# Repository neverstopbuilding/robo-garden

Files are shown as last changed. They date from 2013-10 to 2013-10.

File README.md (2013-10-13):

#RoboGarden

An open source garden hacking project. A robot that will take care of my plants, because I can't. 

Blog posts relating to the development of this project can be found at [http://neverstopbuilding.net/blog/categories/robo-garden](http://neverstopbuilding.net/blog/categories/robo-garden)

##License
<br /><span xmlns:dct="http://purl.org/dc/terms/" property="dct:title">RoboGarden</span> by <span xmlns:cc="http://creativecommons.org/ns#" property="cc:attributionName">Jason Fox</span> is licensed under a <a rel="license" href="http://creativecommons.org/licenses/by-nc-sa/3.0/deed.en_US">Creative Commons Attribution-NonCommercial-ShareAlike 3.0 Unported License</a>.

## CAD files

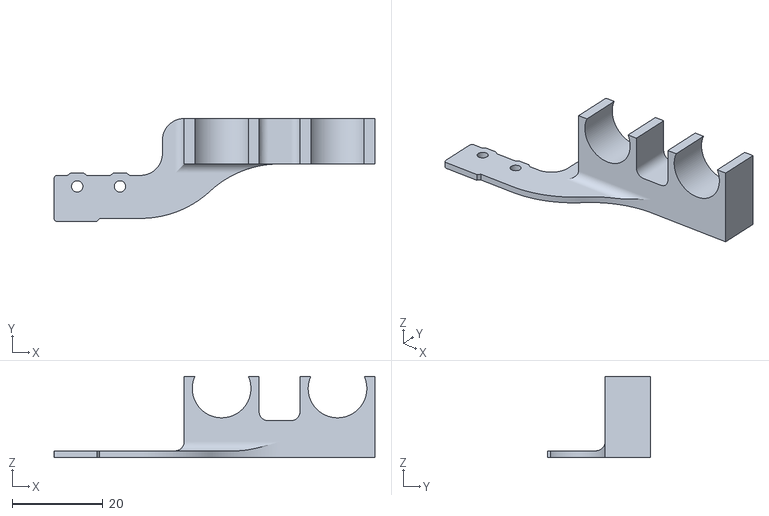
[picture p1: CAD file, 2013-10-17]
3d-parts/micro-clip.stl
70.6 x 22.6 x 17.9

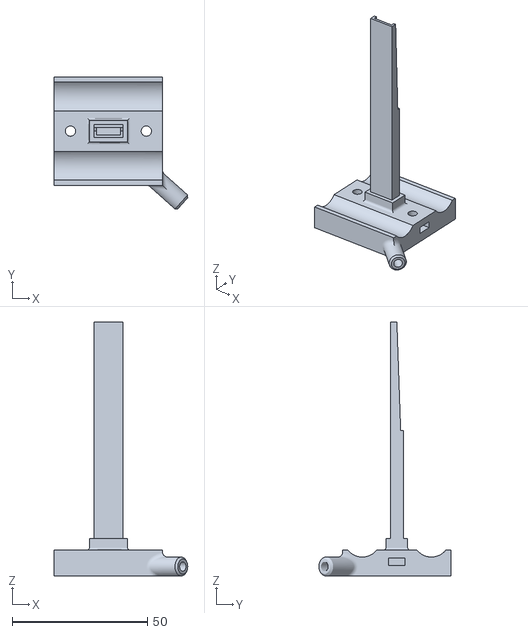
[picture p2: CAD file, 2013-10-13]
3d-parts/carriage-back.stl
49.3 x 48.8 x 93.8

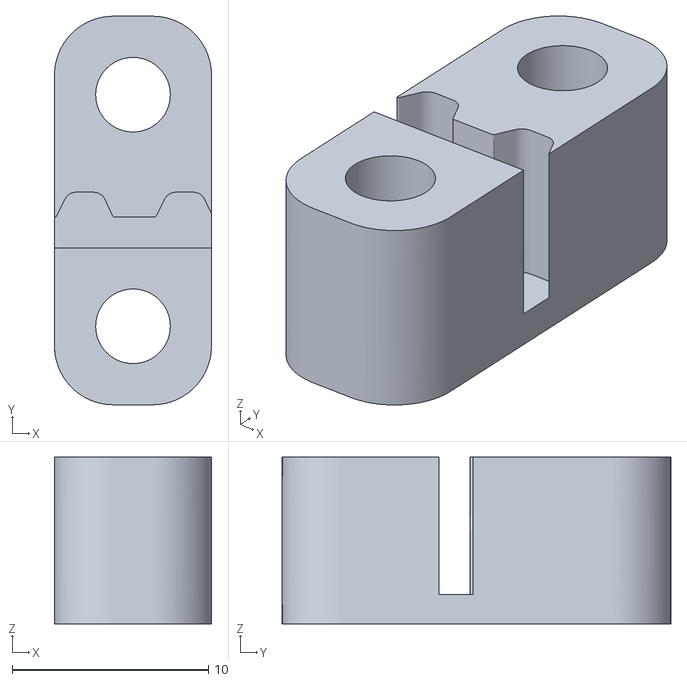
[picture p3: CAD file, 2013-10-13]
3d-parts/belt-clamp.stl
8.00 x 19.8 x 8.50

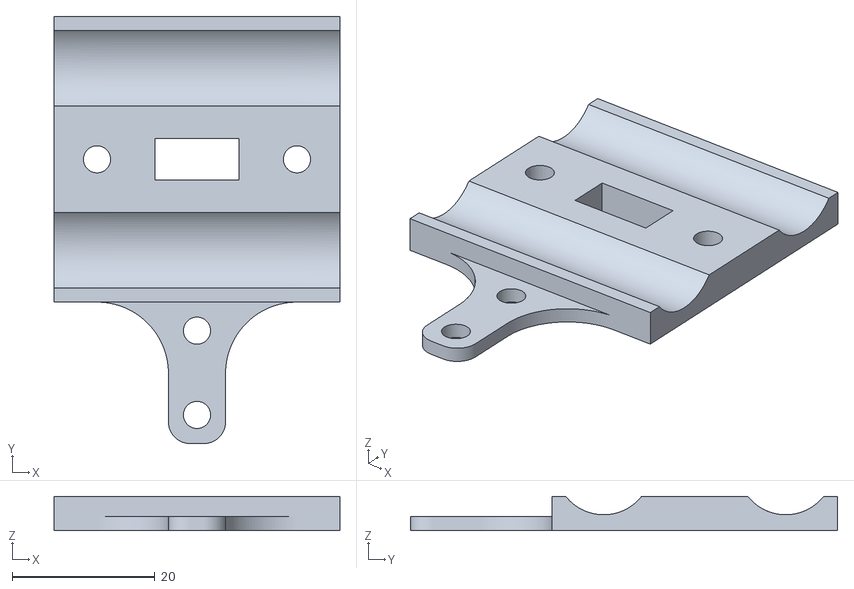
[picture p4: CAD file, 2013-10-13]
3d-parts/carriage-front.stl
40.0 x 59.8 x 4.78

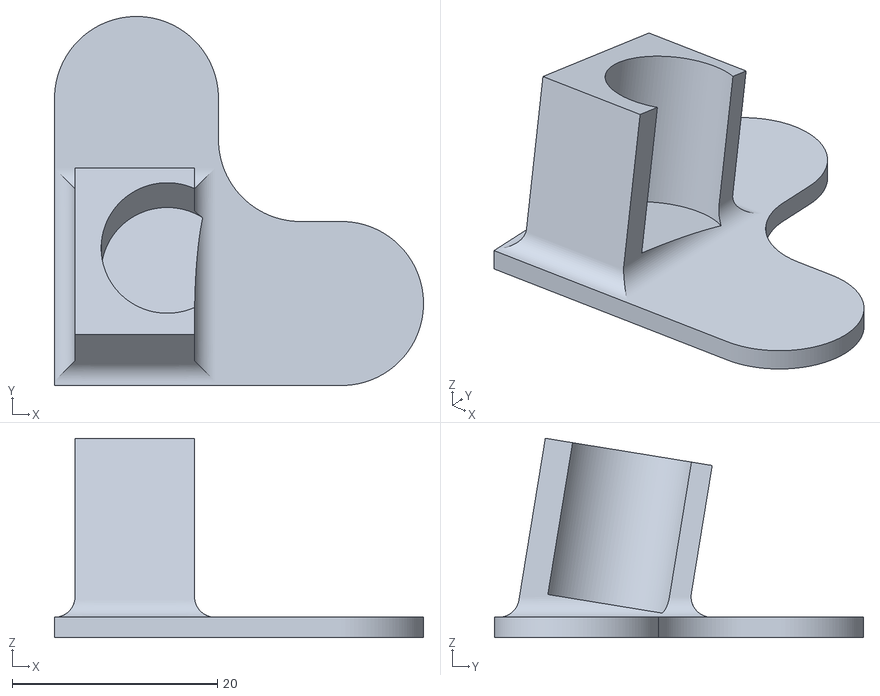
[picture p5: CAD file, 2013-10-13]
3d-parts/foot.stl
36.0 x 36.0 x 19.5

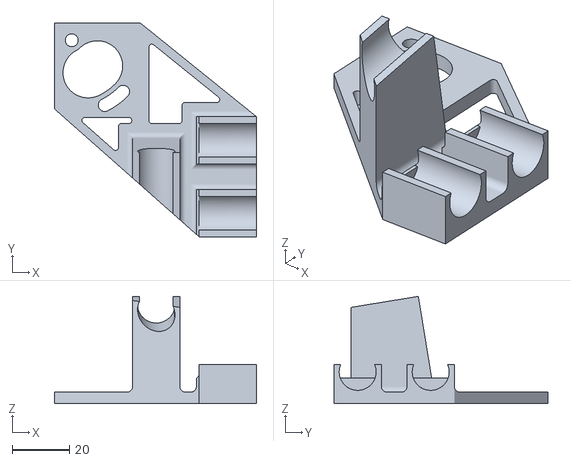
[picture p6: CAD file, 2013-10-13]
3d-parts/idler-mount.stl
70.6 x 74.7 x 37.5

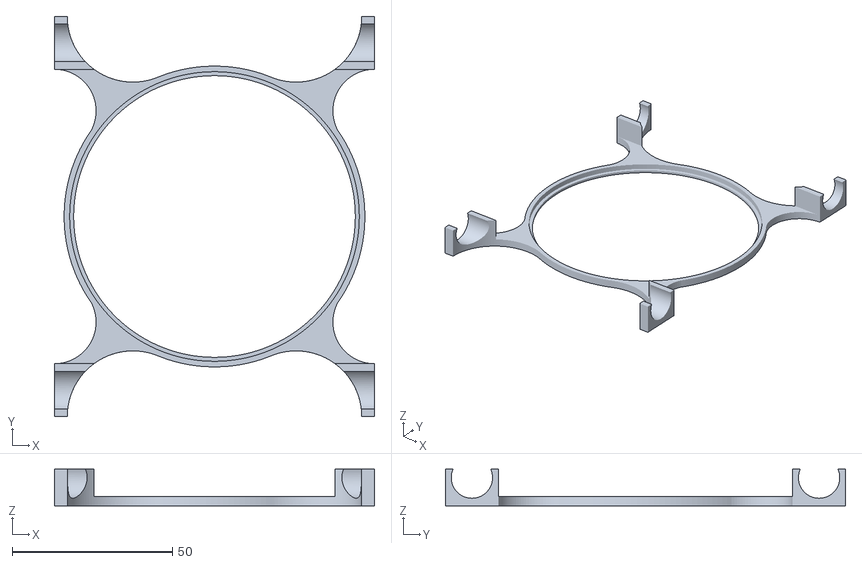
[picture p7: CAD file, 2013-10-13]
3d-parts/light-mount.stl
100.0 x 125.0 x 11.5

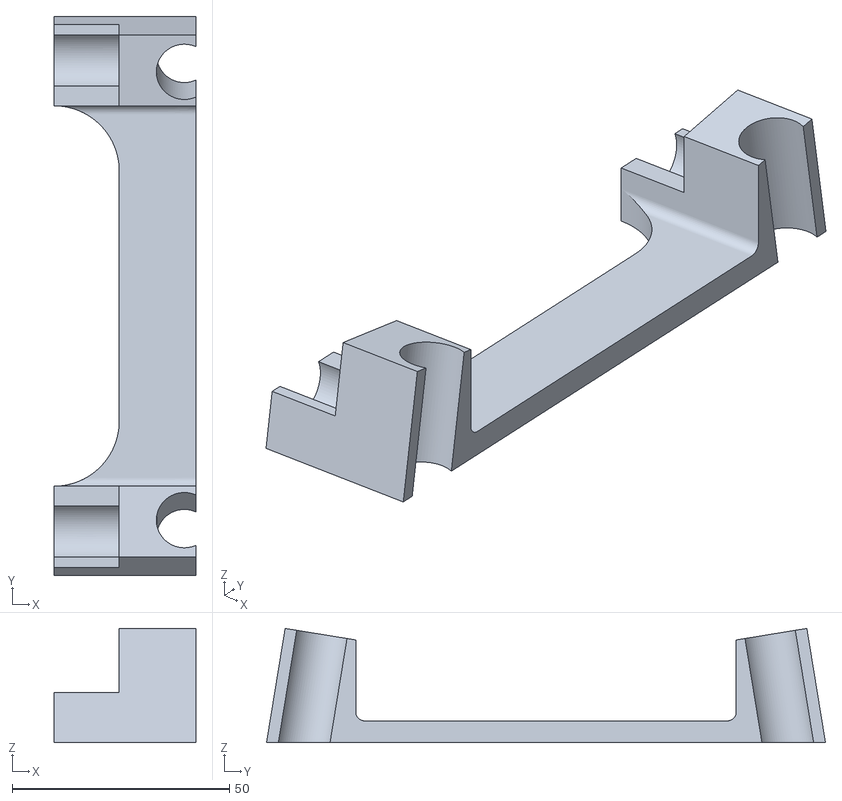
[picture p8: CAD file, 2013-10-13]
3d-parts/top-connector.stl
32.7 x 128.7 x 26.3

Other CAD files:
3d-parts/motor-mount.stl
3d-parts/belt-clamp.ipt
3d-parts/carriage-back.ipt
3d-parts/carriage-front.ipt
3d-parts/foot.ipt
3d-parts/idler-mount.ipt
3d-parts/light-mount.ipt
3d-parts/micro-clip.ipt
3d-parts/motor-mount.ipt
3d-parts/purchased-parts/switch.ipt
3d-parts/rod-long.ipt
3d-parts/rod-short.ipt
3d-parts/top-connector.ipt
robo-gardener-2.iam
robo-gardener-2/Design Accelerator/Synchronous Belt1.ipt
robo-gardener-2/Design Accelerator/Synchronous Belts Transmission1.iam
robo-gardener-2/Design Accelerator/Synchronous Pulley11.ipt
robo-gardener-2/Design Accelerator/Synchronous Pulley21.ipt
robo-gardener.iam
wheel.ipt

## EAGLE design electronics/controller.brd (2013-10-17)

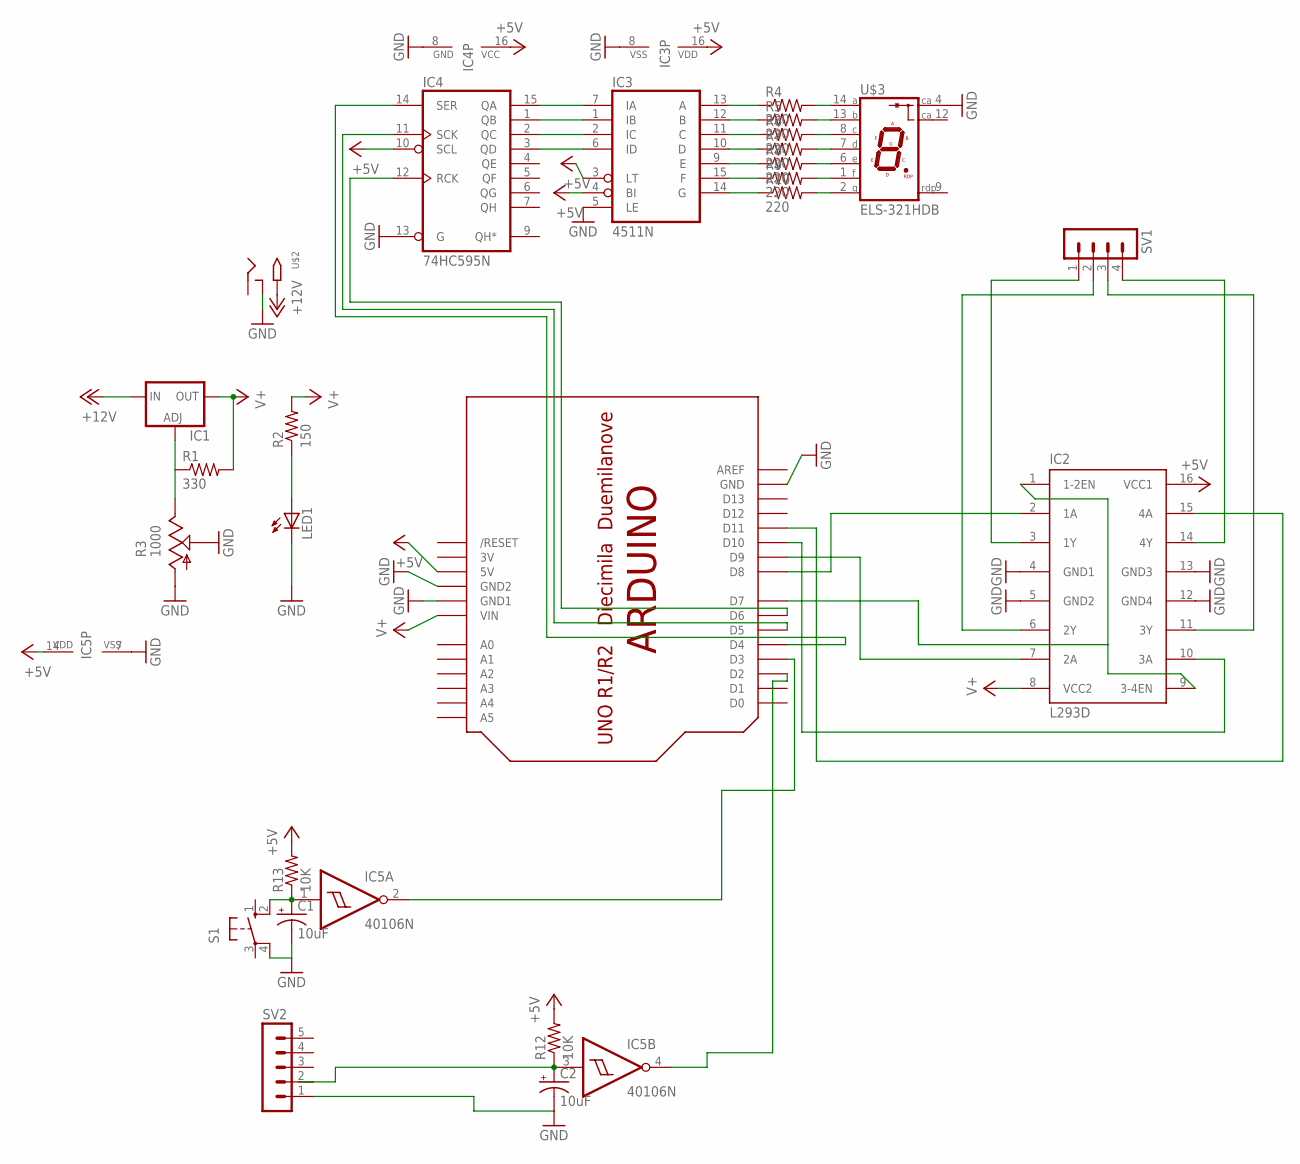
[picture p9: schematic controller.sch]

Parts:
C1, C2: 10uF; E2,5-5
IC1: LM317TS; 317TS
IC2: L293D; DIL16
IC3: 4511N; DIL16
IC4: 74HC595N; DIL16
IC5: 40106N; DIL14
LED1: LED5MM
R1: 330; 0207/10
R2: 150; 0207/10
R3: 1000; LI10
R4, R5, R6, R7, R8, R9, R10: 220; 0207/7
R12, R13: 10K; 0207/7
S1: 10-XX; B3F-10XX
SV1: MA04-1
SV2: MA05-1
U$1: ARDUINO-BPLACE
U$2: 2.1MMJACKTHM; PJ-102A
U$3: ELS-321HDB

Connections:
3V: U$1.3V
+5V: IC2.16 (VCC1), IC3.3 (LT), IC3.4 (BI), IC3.16 (VDD), IC4.10 (SCL), IC4.16 (VCC), IC5.14 (VDD), R12.2, R13.2, U$1.5V
+12V: IC1.3 (IN), U$2.TIP
GND: C1.-, C2.-, IC2.4 (GND1), IC2.5 (GND2), IC2.12 (GND4), IC2.13 (GND3), IC3.5 (LE), IC3.8 (VSS), IC4.8 (GND), IC4.13 (G), IC5.7 (VSS), LED1.K (C), R3.A, R3.S, S1.4 (P1), SV2.1, U$1.GND, U$1.GND1, U$1.GND2, U$2.RING_SW, U$3.4 (C)
unnamed: IC1.1 (ADJ), R1.1, R3.E
unnamed: IC3.13 (A), R4.1
unnamed: LED1.A, R2.1
unnamed: IC2.3 (1Y), SV1.1
unnamed: IC2.6 (2Y), SV1.2
unnamed: IC2.11 (3Y), SV1.3
unnamed: IC2.14 (4Y), SV1.4
unnamed: IC2.2 (1A), U$1.D8
unnamed: IC2.7 (2A), U$1.D9
unnamed: IC2.10 (3A), U$1.D10
unnamed: IC2.15 (4A), U$1.D11
unnamed: IC3.12 (B), R5.1
unnamed: IC2.1 (1-2EN), IC2.9 (3-4EN), U$1.D7
unnamed: IC3.11 (C), R6.1
unnamed: IC3.10 (D), R7.1
unnamed: IC3.9 (E), R8.1
unnamed: IC3.15 (F), R9.1
unnamed: IC3.14 (G), R10.1
unnamed: R4.2, U$3.14 (A)
unnamed: R5.2, U$3.13 (B)
unnamed: R6.2, U$3.8 (C)
unnamed: R7.2, U$3.7 (D)
unnamed: R8.2, U$3.6 (E)
unnamed: R9.2, U$3.1 (F)
unnamed: R10.2, U$3.2 (G)
unnamed: IC3.7 (IA), IC4.15 (QA)
unnamed: IC3.1 (IB), IC4.1 (QB)
unnamed: IC3.2 (IC), IC4.2 (QC)
unnamed: IC3.6 (ID), IC4.3 (QD)
unnamed: IC4.14 (SER), U$1.D4
unnamed: IC4.11 (SCK), U$1.D5
unnamed: IC4.12 (RCK), U$1.D6
unnamed: C1.+, IC5.1 (I), R13.1, S1.2 (S1)
unnamed: IC5.2 (O), U$1.D3
unnamed: C2.+, IC5.3 (I), R12.1, SV2.2
unnamed: IC5.4 (O), U$1.D2
V+: IC1.2 (OUT), IC2.8 (VCC2), R1.2, R2.2, U$1.VIN

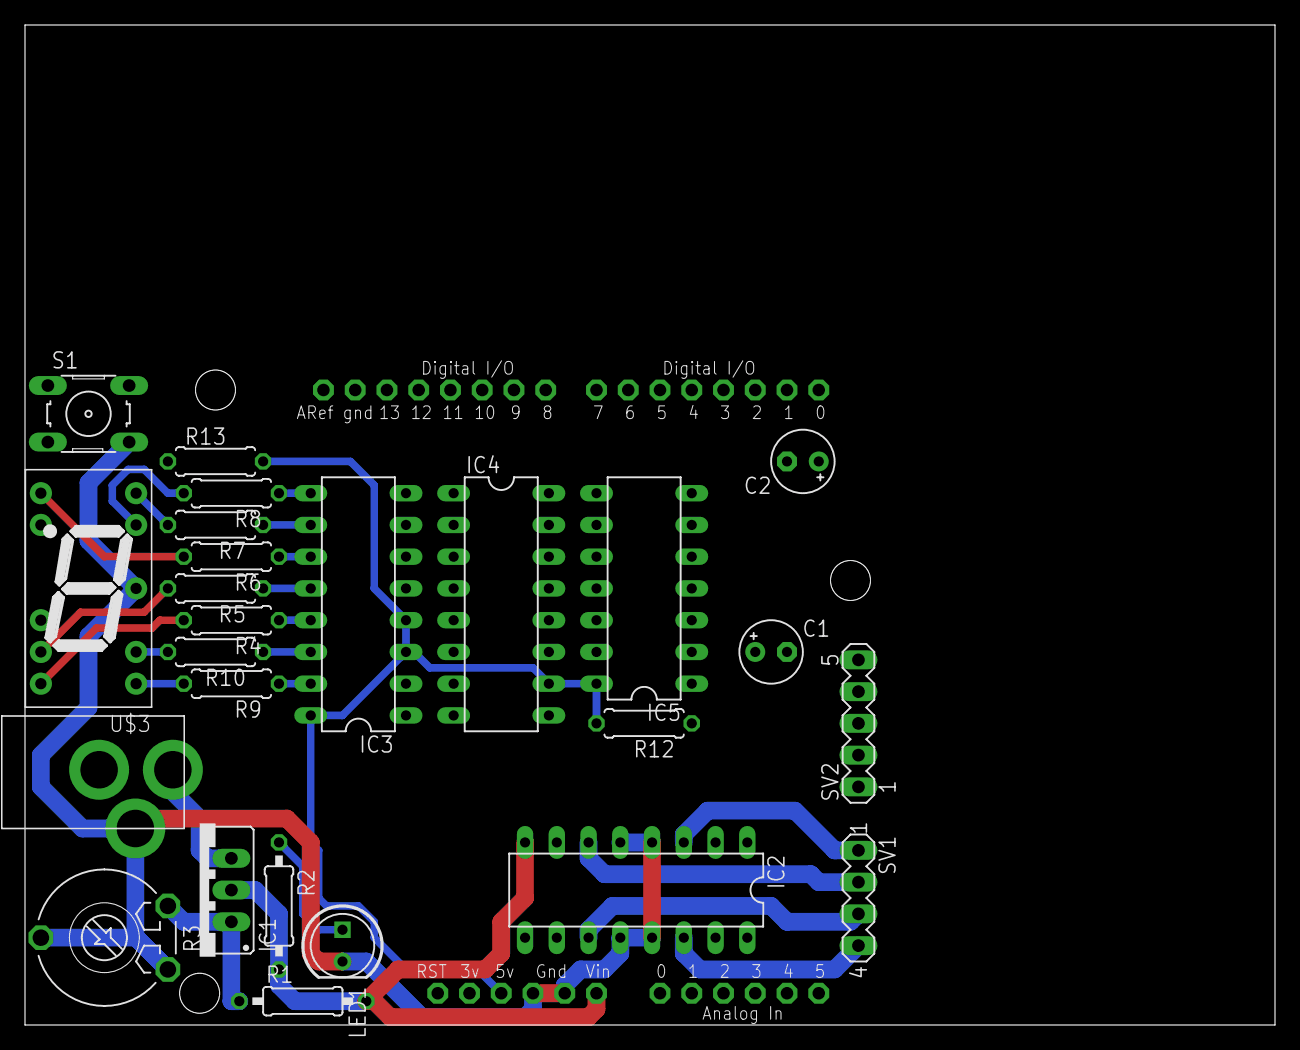
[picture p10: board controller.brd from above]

Board: 2 copper layers, 100.0 x 80.0 mm, 26 parts (0 on the bottom side), 40 nets.

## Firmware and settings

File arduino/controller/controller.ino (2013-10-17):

/* 
 _____       _            _____               _            
|  __ \     | |          / ____|             | |           
| |__) |___ | |__   ___ | |  __  __ _ _ __ __| | ___ _ __  
|  _  // _ \| '_ \ / _ \| | |_ |/ _` | '__/ _` |/ _ \ '_ \ 
| | \ \ (_) | |_) | (_) | |__| | (_| | | | (_| |  __/ | | |
|_|  \_\___/|_.__/ \___/ \_____|\__,_|_|  \__,_|\___|_| |_|
                                                            
RoboGarden Control Software

RoboGarden by Jason Fox is licensed under a Creative Commons Attribution-NonCommercial-ShareAlike 3.0 Unported License.
http://creativecommons.org/licenses/by-nc-sa/3.0/deed.en_US
*/

#include <Stepper.h>

//Global Constants
const int stepsPerRevolution = 200;  //Steps for full revolution of motor
const float stepLength = 0.29066320618892; //Distance carriage moves per step in mm
const int controlSwitchDelay = 1750; //Number of milliseconds since last button press before movement will occur
const float maxDistance = 720; //Maximum distance in mm that the carriage can travel before the other side hits the right end
const int numberOfPlants = 8; //Number of plants between 0 and 8
const float homeOffset = 15; //Distance from homeswitch close where the home would be in mm
const float spoutOffset = 20.46; //distance in mm from the edge of the carriage that hits the home switch and the center of the water spout

//Pins
// Pin 0 Unused
// Pin 1 Unused
int homeSwitch = 0; //Actually into pin 2 but this is the 0th interrupt pin
int controlSwitch = 3;
int shiftRegisterSerial = 4;
int shiftRegisterClock = 5;
int shiftRegisterLatch = 6;
int stepperEnable = 7;
Stepper stepperMotor(stepsPerRevolution, 8,9, 10, 11);     
// Pin 12 Unused
// Pin 13 Unused

//Global and Starting State Variables
int oldControlSwitchState = LOW;
unsigned long controlSwitchTimeOnDown = 0;
unsigned long timeOfLastShortPress = 0;
volatile int displayNumber = 0;
volatile int oldDisplayNumber = 0;
volatile float currentPosition = 0;
volatile float absoluteDistance = maxDistance + homeOffset;
volatile int direction = -1;

//Setup
void setup() {

  //Pin Modes
  attachInterrupt(homeSwitch, resetHomePosition, RISING);
  pinMode(controlSwitch, INPUT);
  pinMode(shiftRegisterSerial, OUTPUT);
  pinMode(shiftRegisterClock, OUTPUT);
  pinMode(shiftRegisterLatch, OUTPUT);
  pinMode(stepperEnable, OUTPUT);

  //Starting State and Settings
  digitalWrite(stepperEnable, LOW);
  stepperMotor.setSpeed(100);
  Serial.begin(9600);
  
  //Print out the plant locations
  printPlantLocations();
}

//Main Loop
void loop() {

  //Movement logic sends carriage to a location based on distance in mm and direction (-1 is right, 1 is left)
  if (absoluteDistance > 0) {
    digitalWrite(stepperEnable, HIGH);
    stepperMotor.step(direction); //Move a single step either right or left based on sign
    if (currentPosition >= maxDistance + spoutOffset) {
      absoluteDistance = 0;
    } else {
      currentPosition += (direction * stepLength);
      absoluteDistance -= stepLength;
      if (absoluteDistance <= 0) {
        Serial.print("Current position: ");
        Serial.println(currentPosition);
      }
    }
  }
  digitalWrite(stepperEnable, LOW);

  //Selection of location logic
  if (displayNumber != oldDisplayNumber && getTimeSinceLastShortPress() > controlSwitchDelay){
    Serial.print("New location: ");
    Serial.println(displayNumber);
    float relativeDistance = getPlantLocation(displayNumber) - currentPosition;
    absoluteDistance = abs(relativeDistance);
    direction = relativeDistance/ abs(relativeDistance);
    oldDisplayNumber = displayNumber;
  }

  //Control switch logic
  int controlSwitchState = digitalRead(controlSwitch);

  if(controlSwitchState != oldControlSwitchState) {
    if (controlSwitchState == HIGH){
      controlSwitchTimeOnDown = millis();
    }
    oldControlSwitchState = controlSwitchState;
  }

  if (controlSwitchTimeOnDown > 0){
    int controlSwitchPressLength = millis() - controlSwitchTimeOnDown;
    if (controlSwitchState == HIGH) {
      if (controlSwitchPressLength >= 1000 ) {
        //Logic on long press
        currentPosition = 0;
        absoluteDistance = maxDistance + homeOffset;
        direction = -1;
        Serial.println("Homing...");

        //Reset logic
        controlSwitchTimeOnDown = 0;
      }
    } else {
      //Logic on short press

      if (displayNumber == 8) {
        displayNumber = 0;
      } else {
        displayNumber++;
      }
      timeOfLastShortPress = millis();
      Serial.print("New display number: ");
      Serial.println(displayNumber);

      //Reset logic
      controlSwitchTimeOnDown = 0;
    }
  }
  setDisplayNumber(displayNumber);

}

//Helper Functions
void setDisplayNumber(int number){
  digitalWrite(shiftRegisterLatch, LOW);
  shiftOut(shiftRegisterSerial, shiftRegisterClock, MSBFIRST, number); 
  digitalWrite(shiftRegisterLatch, HIGH);
}

unsigned long getTimeSinceLastShortPress(){
  if (timeOfLastShortPress == 0){
    return 0;
  } else {
    return millis() - timeOfLastShortPress;
  }
}

float getPlantLocation(int plantNumber){
  if (plantNumber == 0){
    return 0;
  }
  float plantWidth = maxDistance / numberOfPlants;
  return ((plantNumber - 1) * plantWidth ) + (.5 * plantWidth);
}

void printPlantLocations(){
  Serial.println("Please place your plants at these distances from the water spout center at home:");
  for (int p = 1; p <= numberOfPlants; p++){
    Serial.print("Plant ");
    Serial.print(p);
    Serial.print(" at ");
    Serial.print(getPlantLocation(p));
    Serial.println("mm from home.");
  }
}

//Interrupt Functions
void resetHomePosition(){
  direction = 1;
  currentPosition = - homeOffset;
  absoluteDistance = homeOffset;
  displayNumber = 0;
  oldDisplayNumber = 0;
}

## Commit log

2013-10-13 added all the files to the repository
    [Synchronous Belt1.ipt, Synchronous Belts Transmission1.iam, Synchronous Pulley11.ipt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]
2013-10-13 added electronics files
    [controller.brd, controller.sch]
2013-10-16 Updated #robogarden manual control code and schematic
    [controller.brd, controller.sch]
2013-10-17 Updated #RoboGarden code with homing check, refactored the codebase to be cleaner with better comments and variable names, changed logic on button press
    [belt-clamp.ipt, controller.brd, controller.sch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]
